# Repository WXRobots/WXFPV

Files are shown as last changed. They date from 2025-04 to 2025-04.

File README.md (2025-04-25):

# WXFPV
A FPV project for BF &amp; INAV

It include 2 parts for now：
Core Board and Main Board

## Core Board

Core Board is an exchangeable part to apply different MCUs for your ESC，such as AT32F421G8U7，EFM8BB21F16I etc.
The size of this circuit board is fully compatible with mtbsk8's design.
(https://oshwhub.com/mtbsk8/ji-yu-blheli-gu-jian-de-si-he-yi-wu-shua-dian-ji-dian-diao-esc-30-5mm-ban-ben)

EFM8BB21F16I's version can use BLHeli_S firmware
AT32F421G8U7's version can use AM32 firmare

## Main Board

Main Board is an 2-in-1 board，it include a flight controller and a 4-in-1 ESC in One Board.
It is designed to allow for splitting into two pieces for use,for better flexibility,replaceability and maintainability
It can use STM32F405RGT6 or APM32F405RGT6

It is additionally designed with 2 servo PWM interfaces and 3 high-power LED interfaces，so you can connect your servo or filament(or anything you want)to it

In the next upgrade,it will be 3-in-1，added by a communication module

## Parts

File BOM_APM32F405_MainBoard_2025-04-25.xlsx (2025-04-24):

No. | Quantity | Comment | Designator | Footprint | Value | Manufacturer Part | Manufacturer | Supplier Part | Supplier
1 | 1 | AT7456E | AT7456E1 | TSSOP-28_L9.7-W4.4-P0.65-LS6.4-BL-EP-2 |  | AT7456E | 杭州中科微 | C82351 | LCSC
2 | 17 | 100nF | C18,C20,C27,C32,C44,C48,C49,C50,C51,C53,C54,C55,C56,C57,C58,C61,C63 | C0402 | 100nF | CL05B104KB54PNC | SAMSUNG(三星) | C307331 | LCSC
3 | 1 | 1nF | C19 | C0402 | 1nF | 0402B102K500NT | FH(风华) | C1523 | LCSC
4 | 1 | 1uF | C28 | C0402 | 1uF | CL05A105KA5NQNC | SAMSUNG(三星) | C52923 | LCSC
5 | 1 | 100pF | C29 | C0402 | 100pF | 0402CG101J500NT | FH(风华) | C1546 | LCSC
6 | 3 | 2.2uF | C30,C41,C45 | C0402 | 2.2uF | CL05A225MQ5NSNC | SAMSUNG(三星) | C12530 | LCSC
7 | 7 | 10uF | C33,C38,C40,C42,C43,C62,C79 | C0603 | 10uF | CL10A106MA8NRNC | SAMSUNG(三星) | C96446 | LCSC
8 | 3 | 22uF | C46,C47,C65 | C0805 | 22uF | CL21A226MAQNNNE | SAMSUNG(三星) | C45783 | LCSC
9 | 1 | 10nF | C52 | C0402 | 10nF | CL05B103KB5NNNC | SAMSUNG(三星) | C15195 | LCSC
10 | 3 | 4.7uF | C60,C64,C67 | C0805 | 4.7uF | CL21A475KBQNNNE | SAMSUNG(三星) | C98192 | LCSC
11 | 1 | 22pF | C66 | C0402 | 22pF | 0402CG220J500NT | FH(风华) | C1555 | LCSC
12 | 3 | 10uF | C68,C69,C78 | C0603 | 10uF | CL10A106KP8NNNC | SAMSUNG(三星) | C19702 | LCSC
13 | 8 | 10uF | C70,C71,C72,C73,C74,C75,C76,C77 | C1206 | 10uF | CL31A106KBHNNNE | SAMSUNG(三星) | C13585 | LCSC
14 | 2 | MXSH-1.0-08P-WT1-0-A | CN1,CN2 | CONN-SMD_8P-P1.00_MXSH-1.0-08P-WT1-0-A |  | MXSH-1.0-08P-WT1-0-A | MAX(迈旭) | C19185711 | LCSC
15 | 3 | B5819WS | D1,D2,D6 | SOD-323_L1.7-W1.3-LS2.5-FD |  | B5819WS | 宏迦橙 | C7420331 | LCSC
16 | 1 | SD12 | D3 | SOD-323_L1.7-W1.3-LS2.7-RD |  | SD12 | MDD | C502528 | LCSC
17 | 1 | HDR-SMD_8P_P1.27_跨板连接排针 | H1 | HDR-SMD_8P_P1.27-跨板连接排针
18 | 1 | OPTO | H2 | HDR-SMD_5P_P1.27-跨板连接排针
19 | 2 | 10uH | L1,L2 | IND-SMD_L3.0-W3.0-1 | 10uH | CKCSA3010-10uH/M | CENKER(岑科) | C5125973 | LCSC
20 | 1 | 10uH | L3 | IND-SMD_L4.0-W4.0_FNR40XXS | 10uH | MAI4020S-100MT | ceaiya(柯爱亚) | C520273 | LCSC
21 | 1 | PWR | LED1 | LED0603-RD |  | KT-0603R | KENTO | C2286 | LCSC
22 | 1 | LED | LED2 | LED0603-RD |  | NCD0603Y1 | 国星光电 | C84268 | LCSC
23 | 24 | HYG011N04LS2C2 | Q1,Q2,Q3,Q4,Q5,Q6,Q7,Q8,Q9,Q10,Q11,Q12,Q13,Q14,Q15,Q16,Q17,Q18,Q19,Q20,Q21,Q22,Q23,Q24 | TDSON-8_L5.9-W5.2-P1.27-BL |  | HYG011N04LS2C2 |  | C9900088765 | LCSC
24 | 3 | AO3400A | Q25,Q26,Q57 | SOT-23-3_L2.9-W1.3-P1.90-LS2.4-BR |  | AO3400A | AOS | C20917 | LCSC
25 | 1 | HL3401A | Q56 | SOT-23-3_L2.9-W1.3-P1.90-LS2.4-BR |  | HL3401A | 宏嘉诚 | C7420349 | LCSC
26 | 4 | 1kΩ | R1,R4,R15,R109 | R0402 | 1kΩ | 0402WGF1001TCE | UNI-ROYAL(厚声) | C11702 | LCSC
27 | 2 | 4.7kΩ | R2,R3 | R0402 | 4.7kΩ | 0402WGF4701TCE | UNI-ROYAL(厚声) | C25900 | LCSC
28 | 7 | 10kΩ | R5,R6,R14,R17,R19,R20,R116 | R0402 | 10kΩ | 0402WGF1002TCE | UNI-ROYAL(厚声) | C25744 | LCSC
29 | 4 | 22Ω | R10,R11,R12,R13 | R0402 | 22Ω | 0402WGF220JTCE | UNI-ROYAL(厚声) | C25092 | LCSC
30 | 2 | 75Ω | R16,R18 | R0402 | 75Ω | 0402WGF750JTCE | UNI-ROYAL(厚声) | C25133 | LCSC
31 | 1 | 56Ω | R28 | R0402 | 56Ω | RC0402FR-0756RL | YAGEO(国巨) | C137957 | LCSC
32 | 3 | 100kΩ | R29,R110,R113 | R0402 | 100kΩ | TR0402D10K0Q1025Z | EVER OHMS(天二科技) | C149898 | LCSC
33 | 2 | 27kΩ | R30,R112 | R0402 | 27kΩ | 0402WGF2702TCE | UNI-ROYAL(厚声) | C25771 | LCSC
34 | 2 | 2kΩ | R31,R111 | R0402 | 2kΩ | 0402WGF2001TCE | UNI-ROYAL(厚声) | C4109 | LCSC
35 | 1 | 100kΩ | R108 | R0402 | 100kΩ | 0402WGF1003TCE | UNI-ROYAL(厚声) | C25741 | LCSC
36 | 1 | 6.8kΩ | R114 | R0402 | 6.8kΩ | 0402WGF6801TCE | UNI-ROYAL(厚声) | C25917 | LCSC
37 | 1 | 51kΩ | R115 | R0402 | 51kΩ | 0402WGF5102TCE | UNI-ROYAL(厚声) | C25794 | LCSC
38 | 3 | 22Ω | RN1,RN2,RN3 | RES-ARRAY-SMD_0402-8P-L2.0-W1.0-BL | 22Ω | 4D02WGJ0220TCE | UNI-ROYAL(厚声) | C25499 | LCSC
39 | 1 | 1kΩ | RN4 | RES-ARRAY-SMD_0402-8P-L2.0-W1.0-BL | 1kΩ | 4D02WGJ0102TCE | UNI-ROYAL(厚声) | C25726 | LCSC
40 | 1 | Boot | SW1 | KEY-SMD_L3.9-W3.0-LS5.0 |  | BX-TS-26-3929325T | Bossie(博锡) | C18077675 | LCSC
41 | 1 | Bind | SW2 | KEY-SMD_L3.9-W3.0-LS5.0 |  | BX-TS-26-3929325T | Bossie(博锡) | C18077675 | LCSC
42 | 8 | Test-Point | TP1,TP2,TP3,TP4,TP5,TP6,TP7,TP8 | Test-Point-0.5mm
43 | 1 | UART5_RX | TP10 | Test-Point-0.5mm
44 | 1 | UART5_TX | TP12 | Test-Point-0.5mm
45 | 6 | GND | TP14,TP17,TP23,TP30,TP35,TP46 | Test-Point-0.5mm
46 | 6 | 5V | TP16,TP20,TP24,TP26,TP29,TP40 | Test-Point-0.5mm
47 | 1 | SCL | TP19 | Test-Point-0.5mm
48 | 1 | SDA | TP21 | Test-Point-0.5mm
49 | 1 | CAM | TP22 | Test-Point-0.5mm
50 | 1 | PWM1 | TP25 | Test-Point-0.5mm
51 | 1 | PWM2 | TP27 | Test-Point-0.5mm
52 | 1 | ELRS_5V | TP31 | Test-Point-0.5mm
53 | 1 | TX | TP32 | Test-Point-0.5mm
54 | 2 | RX | TP33,TP36 | Test-Point-0.5mm
55 | 1 | Bind | TP34 | Test-Point-0.5mm
56 | 1 | VTX | TP38 | Test-Point-0.5mm
57 | 1 | 12V | TP41 | Test-Point-0.5mm
58 | 1 | LED1 | TP42 | Test-Point-0.5mm
59 | 1 | LED2 | TP43 | Test-Point-0.5mm
60 | 1 | LED3 | TP44 | Test-Point-0.5mm
61 | 3 | VM | TP45,TP47,TP48 | Test-Point-0.5mm
62 | 1 | TP181A2-CR | U1 | SC-70-6_L2.2-W1.3-P0.65-LS2.1-TL |  | TP181A2-CR | 3PEAK(思瑞浦) | C2902350 | LCSC
63 | 1 | 0.5mΩ | U2 | R2512 | 0.5mΩ | EBWM2512FL500S9 | RESI(开步睿思) | C7178835 | LCSC
64 | 1 | APM32F405RGT6 | U3 | LQFP-64_L10.0-W10.0-P0.50-LS12.0-BL |  | APM32F405RGT6 | Geehy(珠海极海) | C5290473 | LCSC
65 | 1 | AP2210K-3.3TRG1 | U4 | SOT-23-5_L3.0-W1.7-P0.95-LS2.8-BR |  | AP2210K-3.3TRG1 | DIODES(美台) | C176959 | LCSC
66 | 2 | JW5026 | U6,U55 | SOT-23-6_L2.9-W1.6-P0.95-LS2.8-BR |  | JW5026 | Joulwatt(杰华特) | C185109 | LCSC
67 | 1 | BLHeli四合一核心板_SJJ | U8 | BLHeli_四合一核心板_SJJ
68 | 1 | SMDJ28CA | U9 | SMC_L6.9-W5.9-LS7.9-BI |  | SMDJ28CA | Liown(里阳半导体) | C2990249 | LCSC
69 | 2 | XC6206P332MR | U10,U11 | SOT-23-3_L3.0-W1.7-P0.95-LS2.9-BR |  | XC6206P332MR | UMW(友台半导体) | C347376 | LCSC
70 | 1 | BMI270 | U12 | LGA-14_L3.0-W2.5-P0.50-BR |  | BMI270 | Bosch(博世) | C2836813 | LCSC
71 | 1 | 27MHz | U13 | OSC-SMD_4P-L2.0-W1.6-BL_X201624MKB4SI | 27MHz | X201627MOB4SI | YXC(扬兴晶振) | C5210654 | LCSC
72 | 1 | BMP280 | U14 | LGA-8_L2.5-W2.0-P0.65_AMP6127 |  | BMP280 | Bosch(博世) | C83291 | LCSC
73 | 1 | W25Q128JVPIQ | U15 | WSON-8_L6.0-W5.0-P1.27-BL-EP |  | W25Q128JVPIQ | WINBOND(华邦) | C190862 | LCSC
74 | 1 | GPS | U16 | CONN-SMD_6P-P1.00_MEGASTAR_ZX-SH1.0-6PWT |  | ZX-SH1.0-6PWT | Megastar(兆星) | C7430448 | LCSC
75 | 1 | Opt | U17 | CONN-SMD_5P-P1.00_MEGASTAR_ZX-SH1.0-5PWT |  | ZX-SH1.0-5PWT | Megastar(兆星) | C7430447 | LCSC
76 | 1 | CAM | U18 | CONN-SMD_3P-P1.00_MEGASTAR_ZX-SH1.0-3PWT |  | ZX-SH1.0-3PWT | Megastar(兆星) | C7430445 | LCSC
77 | 1 | SERVO | U19 | HDR-SMD_6P-P2.54-H-M-R2-C3-LS17.0 |  | PZ254-2-03-WS | HCTL(华灿天禄) | C5149353 | LCSC
78 | 1 | ELRS | U53 | CONN-SMD_4P-P1.00_MEGASTAR_ZX-SH1.0-4PWT |  | ZX-SH1.0-4PWT | Megastar(兆星) | C7430446 | LCSC
79 | 1 | VTX | U54 | CONN-SMD_6P-P1.00_MEGASTAR_ZX-SH1.0-6PWT |  | ZX-SH1.0-6PWT | Megastar(兆星) | C7430448 | LCSC
80 | 1 | SY8292ABC | U56 | SOT-23-6_L2.9-W1.6-P0.95-LS2.8-BR |  | SY8292ABC | silergy(矽力杰) | C83336 | LCSC
81 | 1 | LED | U57 | HDR-SMD_6P-P2.54-H-M-R2-C3-LS17.0 |  | PZ254-2-03-WS | HCTL(华灿天禄) | C5149353 | LCSC
82 | 2 | STHW4-DU-HN2501X510 | U58,U59 | SMD-1_L25.0-W1.5 |  | STHW4-DU-HN2501X510 | STEIPU(斯泰普) | C18548290 | LCSC
83 | 1 | BTC-1022-BN01 | U60 | SMD-2_L10.0-W2.0 |  | BTC-1022-BN01 | BZXC(博众新材) | C20883043 | LCSC
84 | 1 | KH-TYPE-C-16P | USBC1 | USB-C-SMD_KH-TYPE-C-16P |  | KH-TYPE-C-16P | kinghelm(金航标) | C709357 | LCSC
85 | 1 | 8MHz | X1 | OSC-SMD_3P-L3.2-W1.3-P1.2-L | 8MHz | CSTCE8M00G15C99-R0 | muRata(村田) | C110614 | LCSC

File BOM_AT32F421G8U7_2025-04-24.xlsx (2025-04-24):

No. | Quantity | Comment | Designator | Footprint | Value | Manufacturer Part | Manufacturer | Supplier Part | Supplier
1 | 4 | 100nF | C1,C6,C11,C16 | C0201 | 100nF | GRM033R61E104KE14D | muRata(村田) | C76939 | LCSC
2 | 12 | 1uF | C3,C4,C5,C8,C9,C10,C13,C14,C15,C18,C19,C20 | C0402 | 1uF | CL05A105KA5NQNC | SAMSUNG(三星) | C52923 | LCSC
3 | 4 | 4.7uF | C29,C30,C31,C32 | C0402 | 4.7uF | CGA0402X5R475M250GT | HRE(芯声) | C6119795 | LCSC
4 | 12 | 1N4148WT | D1,D2,D3,D4,D5,D6,D7,D8,D9,D10,D11,D12 | SOD-523_L1.2-W0.8-LS1.6-FD |  | 1N4148WT | WPMtek(维攀微) | C2688234 | LCSC
5 | 4 | 220Ω | R1,R19,R37,R55 | R0201 | 220Ω | RC0201FR-07220RL | YAGEO(国巨) | C274342 | LCSC
6 | 24 | 4.7Ω | R4,R5,R6,R7,R10,R15,R21,R23,R24,R25,R26,R29,R39,R41,R42,R43,R44,R49,R58,R59,R60,R61,R62,R67 | R0201 | 4.7Ω | 0201WMJ047JTEE | UNI-ROYAL(厚声) | C473492 | LCSC
7 | 28 | 10kΩ | R8,R9,R11,R12,R13,R14,R27,R28,R30,R31,R32,R33,R45,R46,R47,R48,R50,R51,R63,R64,R65,R66,R68,R69,R73,R74,R75,R76 | R0201 | 10kΩ | 0201WMF1002TEE | UNI-ROYAL(厚声) | C473048 | LCSC
8 | 12 | 1kΩ | R16,R17,R18,R34,R35,R36,R52,R53,R54,R70,R71,R72 | R0201 | 1kΩ | 0201WMF1001TEE | UNI-ROYAL(厚声) | C270365 | LCSC
9 | 1 | 10kΩ | RN1 | RES-ARRAY-SMD_0201-8P-L1.4-W0.6-BL | 10kΩ | 4F01WMJ0103TEE | UNI-ROYAL(厚声) | C2769814 | LCSC
10 | 10 | Test-Point | TP1,TP2,TP3,TP4,TP5,TP6,TP7,TP8,TP9,TP10 | Test-Point-0.5mm
11 | 4 | JSM6288Q | U1,U3,U5,U7 | VQFN-24_L4.0-W4.0-P0.50-TL-EP2.7 |  | JSM6288Q | JSMSEMI(杰盛微) | C19077370 | LCSC
12 | 4 | AT32F421G8U7 | U2,U4,U6,U8 | QFN-28_L4.0-W4.0-P0.40-TL-EP2.4 |  | AT32F421G8U7 | ARTERY(雅特力) | C2765098 | LCSC

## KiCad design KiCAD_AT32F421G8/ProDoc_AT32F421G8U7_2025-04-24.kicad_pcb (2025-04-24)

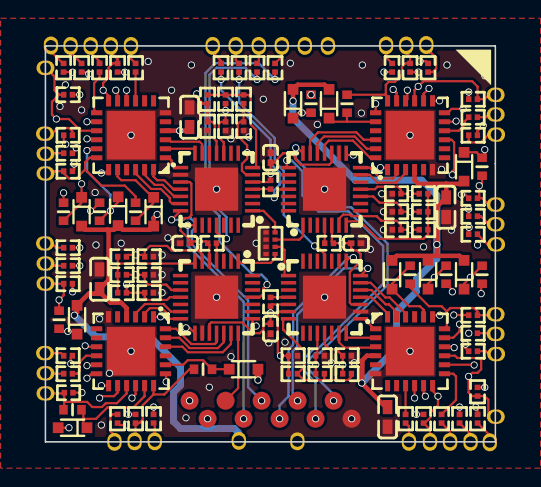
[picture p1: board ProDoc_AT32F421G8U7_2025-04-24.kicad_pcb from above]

Board: 4 copper layers, 25.0 x 22.0 mm, 119 parts (0 on the bottom side), 111 nets.

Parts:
C1, C6, C11, C16: C0201
C3, C4, C5, C8, C9, C10, C13, C14, C15, C18, C19, C20, C29, C30, C31, C32: C0402
D1, D2, D3, D4, D5, D6, D7, D8, D9, D10, D11, D12: SOD-523_L1.2-W0.8-LS1.6-FD
R1, R4, R5, R6, R7, R8, R9, R10, R11, R12, R13, R14, R15, R16, R17, R18, R19, R21, R23, R24, R25, R26, R27, R28, R29, R30, R31, R32, R33, R34, R35, R36, R37, R39, R41, R42, R43, R44, R45, R46, R47, R48, R49, R50, R51, R52, R53, R54, R55, R58, R59, R60, R61, R62, R63, R64, R65, R66, R67, R68, R69, R70, R71, R72, R73, R74, R75, R76: R0201
RN1: RES-ARRAY-SMD_0201-8P-L1.4-W0.6-BL
TP1, TP2, TP3, TP4, TP5, TP6, TP7, TP8, TP9, TP10: Test-Point-0.5mm
U1, U3, U5, U7: VQFN-24_L4.0-W4.0-P0.50-TL-EP2.7
U2, U4, U6, U8: QFN-28_L4.0-W4.0-P0.40-TL-EP2.4

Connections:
3.3V: C1.2, C6.2, C11.2, C16.2, R73.1, R74.1, R75.1, R76.1, TP10.1, U2.5, U2.17, U4.5, U4.17, U6.5, U6.17, U8.5, U8.17
12V: C29.2, C30.2, C31.2, C32.2, D1.1, D2.1, D3.1, D4.1, D5.1, D6.1, D7.1, D8.1, D9.1, D10.1, D11.1, D12.1, U1.4, U3.4, U5.4, U7.4
$1N5017: R1.1, U2.25
$1N5688: R73.2, U2.4
$2N3149: R19.1, U4.25
$2N3240: R74.2, U4.4
$3N2377: R37.1, U6.25
$3N3106: R75.2, U6.4
$4N2377: R55.1, U8.25
$4N3105: R76.2, U8.4
BOOT1: RN1.5, U2.1
BOOT2: RN1.8, U4.1
BOOT3: RN1.6, U6.1
BOOT4: RN1.7, U8.1
GND: C1.1, C6.1, C11.1, C16.1, C29.1, C30.1, C31.1, C32.1, R16.1, R17.1, R18.1, R34.1, R35.1, R36.1, R52.1, R53.1, R54.1, R70.1, R71.1, R72.1, RN1.1, RN1.2, RN1.3, RN1.4, TP9.1, U1.6, U1.25, U2.16, U2.29, U3.6, U3.25, U4.16, U4.29, U5.6, U5.25, U6.16, U6.29, U7.6, U7.25, U8.16, U8.29
M1_AH: U1.22, U2.20
M1_AL: U1.1, U2.15
M1_BH: U1.23, U2.19
M1_BL: U1.2, U2.14
M1_CH: U1.24, U2.18
M1_CL: U1.3, U2.13
M1_HO1: R4.1, U1.19
M1_HO2: R5.1, U1.16
M1_HO3: R6.1, U1.13
M1_LO1: R7.1, U1.11
M1_LO2: R10.1, U1.10
M1_LO3: R15.1, U1.9
M1_SEN_A: R8.2, R9.1, R18.2, U2.6
M1_SEN_B: R11.2, R12.1, R17.2, U2.10
M1_SEN_C: R13.2, R14.1, R16.2, U2.11
M1_SEN_COM: R8.1, R11.1, R13.1, U2.7
M1_SWCLK: TP1.1, U2.22
M1_SWDIO: TP2.1, U2.21
M1_VB1: C3.1, D1.2, U1.20
M1_VB2: C4.1, D2.2, U1.17
M1_VB3: C5.1, D3.2, U1.14
M1_VS1: C3.2, R9.2, U1.18
M1_VS2: C4.2, R12.2, U1.15
M1_VS3: C5.2, R14.2, U1.12
M2_AH: U3.22, U4.20
M2_AL: U3.1, U4.15
M2_BH: U3.23, U4.19
M2_BL: U3.2, U4.14
M2_CH: U3.24, U4.18
M2_CL: U3.3, U4.13
M2_HO1: R21.1, U3.19
M2_HO2: R23.1, U3.16
M2_HO3: R24.1, U3.13
M2_LO1: R25.1, U3.11
M2_LO2: R26.1, U3.10
M2_LO3: R29.1, U3.9
M2_SEN_A: R27.2, R28.1, R36.2, U4.6
M2_SEN_B: R30.2, R31.1, R35.2, U4.10
M2_SEN_C: R32.2, R33.1, R34.2, U4.11
M2_SEN_COM: R27.1, R30.1, R32.1, U4.7
M2_SWCLK: TP3.1, U4.22
M2_SWDIO: TP4.1, U4.21
M2_VB1: C8.1, D4.2, U3.20
M2_VB2: C9.1, D5.2, U3.17
M2_VB3: C10.1, D6.2, U3.14
M2_VS1: C8.2, R28.2, U3.18
M2_VS2: C9.2, R31.2, U3.15
M2_VS3: C10.2, R33.2, U3.12
M3_AH: U5.22, U6.20
M3_AL: U5.1, U6.15
M3_BH: U5.23, U6.19
M3_BL: U5.2, U6.14
M3_CH: U5.24, U6.18
M3_CL: U5.3, U6.13
M3_HO1: R39.1, U5.19
M3_HO2: R41.1, U5.16
M3_HO3: R42.1, U5.13
M3_LO1: R43.1, U5.11
M3_LO2: R44.1, U5.10
M3_LO3: R49.1, U5.9
M3_SEN_A: R45.2, R46.1, R54.2, U6.6
M3_SEN_B: R47.2, R48.1, R53.2, U6.10
M3_SEN_C: R50.2, R51.1, R52.2, U6.11
M3_SEN_COM: R45.1, R47.1, R50.1, U6.7
M3_SWCLK: TP5.1, U6.22
M3_SWDIO: TP6.1, U6.21
M3_VB1: C13.1, D7.2, U5.20
M3_VB2: C14.1, D8.2, U5.17
M3_VB3: C15.1, D9.2, U5.14
M3_VS1: C13.2, R46.2, U5.18
M3_VS2: C14.2, R48.2, U5.15
M3_VS3: C15.2, R51.2, U5.12
M4_AH: U7.22, U8.20
M4_AL: U7.1, U8.15
M4_BH: U7.23, U8.19
M4_BL: U7.2, U8.14
M4_CH: U7.24, U8.18
M4_CL: U7.3, U8.13
M4_HO1: R58.1, U7.19
M4_HO2: R59.1, U7.16
M4_HO3: R60.1, U7.13
M4_LO1: R61.1, U7.11
M4_LO2: R62.1, U7.10
M4_LO3: R67.1, U7.9
M4_SEN_A: R63.2, R64.1, R72.2, U8.6
M4_SEN_B: R65.2, R66.1, R71.2, U8.10
M4_SEN_C: R68.2, R69.1, R70.2, U8.11
M4_SEN_COM: R63.1, R65.1, R68.1, U8.7
M4_SWCLK: TP7.1, U8.22
M4_SWDIO: TP8.1, U8.21
M4_VB1: C18.1, D10.2, U7.20
M4_VB2: C19.1, D11.2, U7.17
M4_VB3: C20.1, D12.2, U7.14
M4_VS1: C18.2, R64.2, U7.18
M4_VS2: C19.2, R66.2, U7.15
M4_VS3: C20.2, R69.2, U7.12

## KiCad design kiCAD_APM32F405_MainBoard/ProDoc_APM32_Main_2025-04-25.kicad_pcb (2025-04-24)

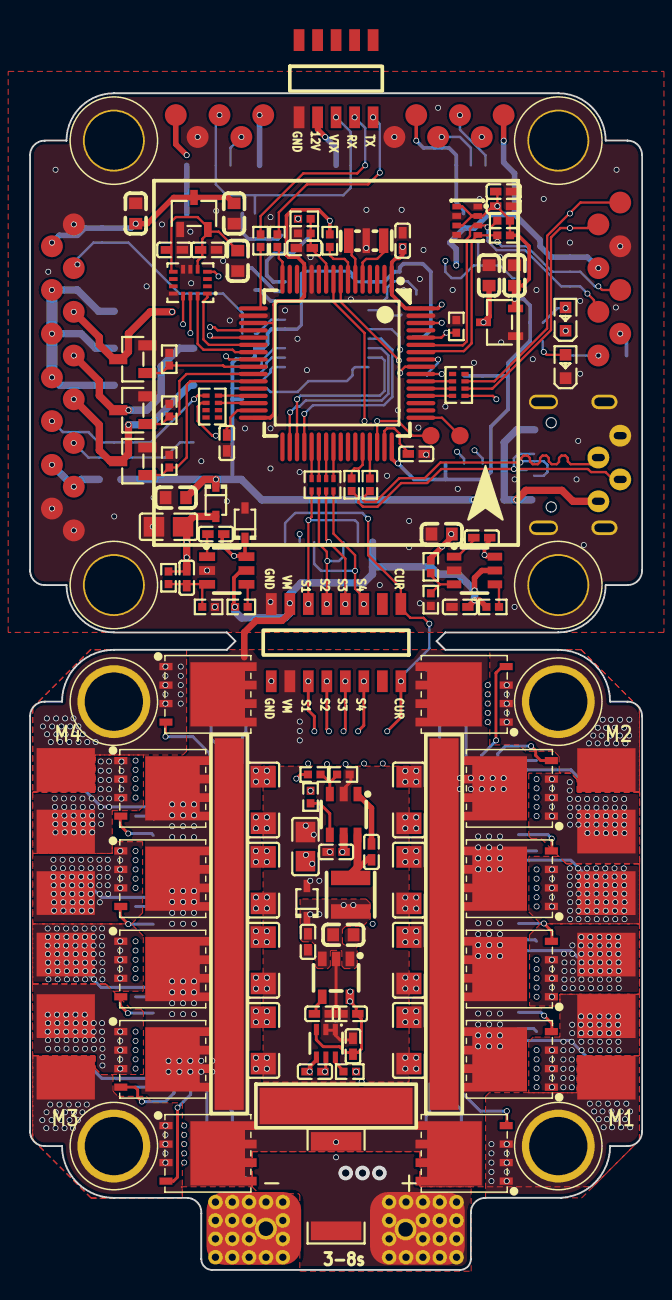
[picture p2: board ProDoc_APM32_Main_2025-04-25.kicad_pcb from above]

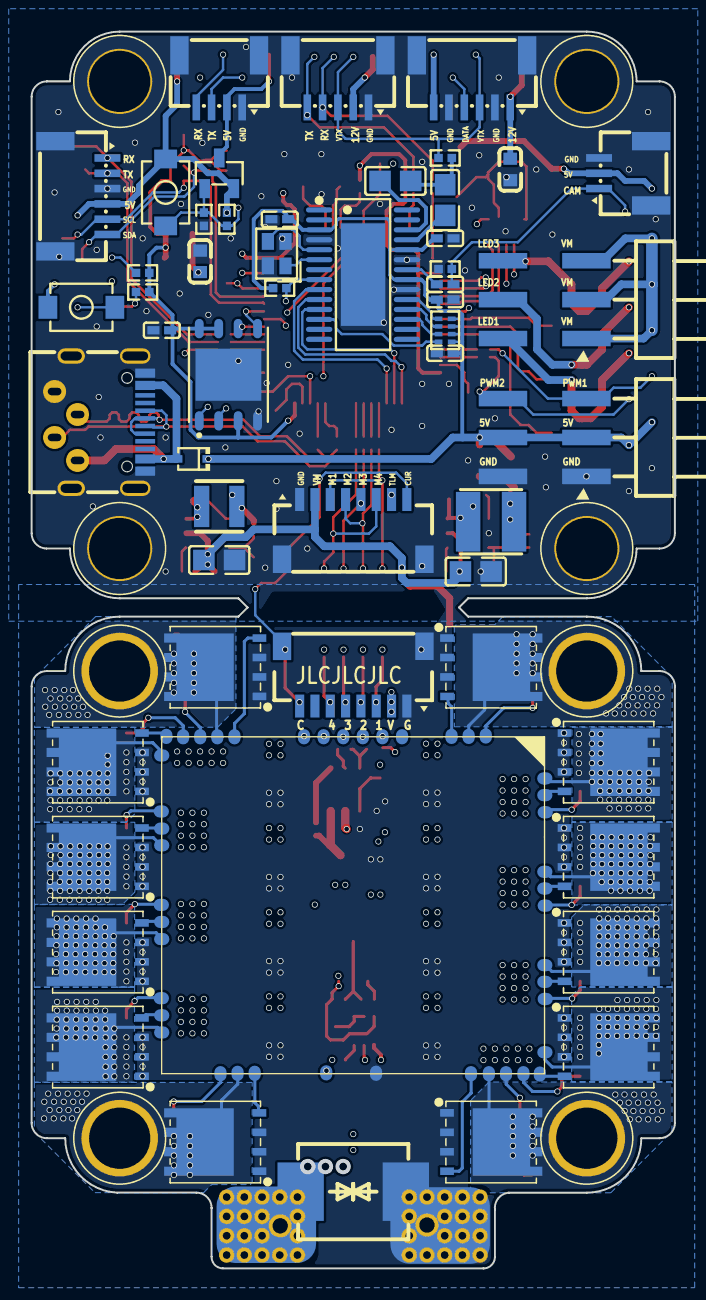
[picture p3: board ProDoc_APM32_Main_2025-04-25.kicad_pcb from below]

Board: 6 copper layers, 42.0 x 80.8 mm, 194 parts (59 on the bottom side), 136 nets.

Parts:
AT7456E1: TSSOP-28_L9.7-W4.4-P0.65-LS6.4-BL-EP-2
C18, C19, C20, C27, C28, C29, C30, C32, C41, C44, C45, C48, C49, C50, C51, C52, C53, C54, C55, C56, C57, C58, C61, C63, C66: C0402
C33, C38, C40, C42, C43, C62, C68, C69, C78, C79: C0603
C46, C47, C60, C64, C65, C67: C0805
C70, C71, C72, C73, C74, C75, C76, C77: C1206
CN1, CN2: CONN-SMD_8P-P1.00_MXSH-1.0-08P-WT1-0-A
D1, D2, D6: SOD-323_L1.7-W1.3-LS2.5-FD
D3: SOD-323_L1.7-W1.3-LS2.7-RD
H1: HDR-SMD_8P_P1.27-跨板连接排针
H2: HDR-SMD_5P_P1.27-跨板连接排针
L1, L2: IND-SMD_L3.0-W3.0-1
L3: IND-SMD_L4.0-W4.0_FNR40XXS
LED1, LED2: LED0603-RD
Q1, Q2, Q3, Q4, Q5, Q6, Q7, Q8, Q9, Q10, Q11, Q12, Q13, Q14, Q15, Q16, Q17, Q18, Q19, Q20, Q21, Q22, Q23, Q24: TDSON-8_L5.9-W5.2-P1.27-BL
Q25, Q26, Q56, Q57: SOT-23-3_L2.9-W1.3-P1.90-LS2.4-BR
R1, R2, R3, R4, R5, R6, R10, R11, R12, R13, R14, R15, R16, R17, R18, R19, R20, R28, R29, R30, R31, R108, R109, R110, R111, R112, R113, R114, R115, R116: R0402
RN1, RN2, RN3, RN4: RES-ARRAY-SMD_0402-8P-L2.0-W1.0-BL
SW1, SW2: KEY-SMD_L3.9-W3.0-LS5.0
TP1, TP2, TP3, TP4, TP5, TP6, TP7, TP8, TP10, TP12, TP14, TP16, TP17, TP19, TP20, TP21, TP22, TP23, TP24, TP25, TP26, TP27, TP29, TP30, TP31, TP32, TP33, TP34, TP35, TP36, TP38, TP40, TP41, TP42, TP43, TP44, TP45, TP46, TP47, TP48: Test-Point-0.5mm
U1: SC-70-6_L2.2-W1.3-P0.65-LS2.1-TL
U2: R2512
U3: LQFP-64_L10.0-W10.0-P0.50-LS12.0-BL
U4: SOT-23-5_L3.0-W1.7-P0.95-LS2.8-BR
U6, U55, U56: SOT-23-6_L2.9-W1.6-P0.95-LS2.8-BR
U8: BLHeli_四合一核心板_SJJ
U9: SMC_L6.9-W5.9-LS7.9-BI
U10, U11: SOT-23-3_L3.0-W1.7-P0.95-LS2.9-BR
U12: LGA-14_L3.0-W2.5-P0.50-BR
U13: OSC-SMD_4P-L2.0-W1.6-BL_X201624MKB4SI
U14: LGA-8_L2.5-W2.0-P0.65_AMP6127
U15: WSON-8_L6.0-W5.0-P1.27-BL-EP
U16, U54: CONN-SMD_6P-P1.00_MEGASTAR_ZX-SH1.0-6PWT
U17: CONN-SMD_5P-P1.00_MEGASTAR_ZX-SH1.0-5PWT
U18: CONN-SMD_3P-P1.00_MEGASTAR_ZX-SH1.0-3PWT
U19, U57: HDR-SMD_6P-P2.54-H-M-R2-C3-LS17.0
U53: CONN-SMD_4P-P1.00_MEGASTAR_ZX-SH1.0-4PWT
U58, U59: SMD-1_L25.0-W1.5
U60: SMD-2_L10.0-W2.0
USBC1: USB-C-SMD_KH-TYPE-C-16P
X1: OSC-SMD_3P-L3.2-W1.3-P1.2-L

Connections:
3V3: C27.1, C38.2, C48.1, C49.1, C51.1, R1.2, R2.2, R3.2, R4.2, R6.2, SW1.2, TP8.1, U3.1, U3.13, U3.19, U3.32, U3.48, U3.64, U10.2, U14.2, U14.6, U14.8, U15.3, U15.7, U15.8
3V3_GYRO: C43.2, C52.2, C53.2, U11.2, U12.5, U12.8
5V: AT7456E1.3, AT7456E1.21, AT7456E1.24, C40.2, C42.2, C54.2, C55.2, C56.2, C57.2, C68.2, C69.2, C78.2, D1.2, D2.2, Q56.2, R17.2, R108.2, RN4.5, RN4.6, RN4.7, RN4.8, SW2.1, TP16.1, TP20.1, TP24.1, TP26.1, TP29.1, U10.3, U11.3, U16.4, U18.2, U19.3, U19.4
12V: C28.2, C33.2, D3.1, L1.2, R30.2, U4.1, U4.3, U8.14
$1N5871: C20.1, U6.1
$1N5872: R29.2, U6.4
$1N5875: R30.1, R31.2, U6.3
$1N5876: C20.2, L1.1, U6.6
$1N5882: C29.2, U4.4
$3N1830: R28.1, U1.6
$4N5037: R6.1, U3.7
$4N5056: C45.1, U3.31
$4N5066: C41.1, U3.47
$4N5110: AT7456E1.6, U13.1
$4N5111: AT7456E1.5, U13.3
$4N5116: AT7456E1.22, C50.2
$4N5118: C46.2, C47.2, R16.1
$4N5119: AT7456E1.25, C47.1
$4N5120: AT7456E1.26, C46.1
$4N5162: LED2.2, R4.1
$4N5163: LED1.2, R1.1
$4N5203: RN1.3, U3.54
$4N5204: RN1.2, U3.53
$4N5218: R10.1, U3.16
$4N5219: R11.1, U3.17
$4N5327: AT7456E1.12, RN4.1
$4N5328: AT7456E1.17, RN4.2
$4N5329: AT7456E1.18, RN4.3
$4N5330: AT7456E1.19, RN4.4
$4N14776: C58.1, U55.1
$4N14777: R110.2, U55.4
$4N14780: R111.2, R112.1, U55.3
$4N14781: C58.2, L2.1, U55.6
$4N15508: C63.2, D6.2, L3.1, U56.6
$4N15513: C63.1, U56.1
$4N15879: R113.2, U56.4
$4N16265: C66.1, R114.2, R115.1, U56.3
+3.3V: C18.1, C30.2, U1.3, U4.5, U8.35
ADC_CUR: CN1.8, CN1.9, CN2.8, H1.1, R28.2, U3.9
ADC_VBAT: C44.1, R14.1, R15.2, U3.10
AH_1: Q1.4, U8.11
AH_2: Q7.4, U8.2
AH_3: Q13.4, U8.22
AH_4: Q19.4, U8.31
AL_1: Q2.4, U8.13
AL_2: Q8.4, U8.3
AL_3: Q14.4, U8.23
AL_4: Q20.4, U8.33
A_1: Q1.1, Q1.2, Q1.3, Q2.5, U8.12
A_2: Q7.1, Q7.2, Q7.3, Q8.5, U8.4
A_3: Q13.1, Q13.2, Q13.3, Q14.5, U8.24
A_4: Q19.1, Q19.2, Q19.3, Q20.5, U8.32
BH_1: Q3.4, U8.8
BH_2: Q9.4, U8.43
BH_3: Q15.4, U8.19
BH_4: Q21.4, U8.28
BIND: Q56.1, R108.1, R109.2, SW2.2, TP34.1
BL_1: Q4.4, U8.9
BL_2: Q10.4, U8.44
BL_3: Q16.4, U8.20
BL_4: Q22.4, U8.29
BOOT0: R5.1, SW1.1, TP7.1, U3.60
BOX_CS: U3.8, U15.1
BOX_MISO: U3.56, U15.2
BOX_MOSI: U3.57, U15.5
BOX_SCK: U3.55, U15.6
B_1: Q3.1, Q3.2, Q3.3, Q4.5, U8.10
B_2: Q9.1, Q9.2, Q9.3, Q10.5, U8.1
B_3: Q15.1, Q15.2, Q15.3, Q16.5, U8.21
B_4: Q21.1, Q21.2, Q21.3, Q22.5, U8.30
CAM: C50.1, R18.2, TP22.1, U18.1
CH_1: Q5.4, U8.5
CH_2: Q11.4, U8.42
CH_3: Q17.4, U8.18
CH_4: Q23.4, U8.25
CL_1: Q6.4, U8.6
CL_2: Q12.4, U8.40
CL_3: Q18.4, U8.16
CL_4: Q24.4, U8.26
C_1: Q5.1, Q5.2, Q5.3, Q6.5, U8.7
C_2: Q11.1, Q11.2, Q11.3, Q12.5, U8.41
C_3: Q17.1, Q17.2, Q17.3, Q18.5, U8.17
C_4: Q23.1, Q23.2, Q23.3, Q24.5, U8.27
D+: R13.2, TP5.1, USBC1.A6, USBC1.B6
D-: R12.2, TP3.1, USBC1.A7, USBC1.B7
DC_5V: C65.1, C66.2, D2.1, L3.2, R115.2
DM: R12.1, U3.44
DP: R13.1, U3.45
ELRS_5V: Q56.3, TP31.1, U53.2
ESC_S1: CN1.3, CN2.3, H1.6, RN2.8, U8.38
ESC_S2: CN1.4, CN2.4, H1.5, RN2.7, U8.39
ESC_S3: CN1.5, CN2.5, H1.4, RN2.6, U8.36
ESC_S4: CN1.6, CN2.6, H1.3, RN2.5, U8.37
GND: AT7456E1.4, AT7456E1.20, AT7456E1.23, AT7456E1.29, C18.2, C27.2, C28.1, C29.1, C30.1, C32.1, C33.1, C38.1, C40.1, C41.2, C42.1, C43.1, C44.2, C45.2, C48.2, C49.2, C51.2, C52.1, C53.1, C54.1, C55.1, C56.1, C57.1, C60.1, C61.1, C62.1, C64.1, C65.2, C67.1, C68.1, C69.1, C70.1, C71.1, C72.1, C73.1, C74.1, C75.1, C76.1, C77.1, C78.1, C79.1, CN1.1, CN1.10, CN2.1, CN2.9, CN2.10, D3.2, D6.1, H1.8, H2.1, LED1.1, Q2.1, Q2.2, Q2.3, Q4.1, Q4.2, Q4.3, Q6.1, Q6.2, Q6.3, Q8.1, Q8.2, Q8.3, Q10.1, Q10.2, Q10.3, Q12.1, Q12.2, Q12.3, Q14.1, Q14.2, Q14.3, Q16.1, Q16.2, Q16.3, Q18.1, Q18.2, Q18.3, Q20.1, Q20.2, Q20.3, Q22.1, Q22.2, Q22.3, Q24.1, Q24.2, Q24.3, Q25.2, Q26.2, Q57.2, R5.2, R15.1, R18.1, R19.1, R20.1, R31.1, R109.1, R111.1, R114.1, R116.1, TP6.1, TP14.1, TP17.1, TP23.1, TP30.1, TP35.1, TP46.1, U1.1, U1.2, U3.12, U3.18, U3.63, U4.2, U6.2, U8.15, U9.1, U10.1, U11.1, U12.6, U12.7, U12.11, U13.2, U13.4, U14.1, U14.5, U14.7, U15.4, U15.9, U16.3, U16.7, U16.8, U17.1, U17.6, U17.7, U18.3, U18.4, U18.5, U19.1, U19.2, U53.1, U53.5, U53.6, U54.2, U54.5, U54.7, U54.8, U55.2, U56.2, USBC1.1, USBC1.2, USBC1.3, USBC1.4, USBC1.A1, USBC1.A12, USBC1.B1, USBC1.B12, X1.2
GYRO1_CS: U3.20, U12.12
GYRO1_EXTI: U3.24, U12.4
I2C1_SCL: R2.1, TP19.1, U3.58, U14.4, U16.5
I2C1_SDA: R3.1, TP21.1, U3.59, U14.3, U16.6
LED: LED2.1, U3.62
LED1_GATE: Q25.1, R19.2, U3.27
LED1_OUT: Q25.3, TP42.1, U57.2
LED2_GATE: Q26.1, R20.2, U3.26
LED2_OUT: Q26.3, TP43.1, U57.4
LED3_GATE: Q57.1, R116.2, U3.25
LED3_OUT: Q57.3, TP44.1, U57.6
MOTOR1: RN2.1, U3.37
MOTOR2: RN2.2, U3.38
MOTOR3: RN2.3, U3.39
MOTOR4: RN2.4, U3.40
MOTOR7: RN3.5, U3.29
MOTOR8: RN3.6, U3.30
OSC_IN: U3.5, X1.3
OSC_OUT: U3.6, X1.1
OSD_CS: AT7456E1.8, R17.1, TP4.1, U3.46
PWM1: RN3.4, TP25.1, U19.5
PWM2: RN3.3, TP27.1, U19.6
SPI1_SCK: U3.21, U12.13
SPI1_SDI: U3.22, U12.1
SPI1_SDO: U3.23, U12.14
SPI2_SCK: AT7456E1.10, U3.34
SPI2_SDI: AT7456E1.11, U3.35
SPI2_SDO: AT7456E1.9, U3.36
SWCLK: TP1.1, U3.49
TLM: CN2.7, RN1.8
UART2_RX: H2.4, R11.2, TP33.1, U17.4, U53.4
UART2_TX: H2.5, R10.2, TP32.1, U17.5, U53.3
UART3_RX: RN1.1, U3.52
UART5_RX: RN1.6, TP10.1, U16.1
UART5_TX: RN1.7, TP12.1, U16.2
USB_5V: D1.1, TP2.1, USBC1.A4, USBC1.A9, USBC1.B4, USBC1.B9
VBAT: C19.1, U1.4, U2.1, U9.2
VM: C19.2, C32.2, C60.2, C61.2, C64.2, C67.2, C70.2, C71.2, C72.2, C73.2, C74.2, C75.2, C76.2, C77.2, CN1.2, CN2.2, H1.7, Q1.5, Q3.5, Q5.5, Q7.5, Q9.5, Q11.5, Q13.5, Q15.5, Q17.5, Q19.5, Q21.5, Q23.5, R14.2, R29.1, R110.1, R113.1, TP45.1, TP47.1, TP48.1, U1.5, U2.2, U6.5, U55.5, U56.5, U57.1, U57.3, U57.5, U58.1, U59.1, U60.1
VTX: H2.3, R16.2, TP38.1, U17.3, U54.3
VTX_5VOUT: TP40.1, U54.6
VTX_12V: C62.2, C79.2, H2.2, L2.2, R112.2, TP41.1, U17.2, U54.1
VTX_RX: TP36.1, U54.4
